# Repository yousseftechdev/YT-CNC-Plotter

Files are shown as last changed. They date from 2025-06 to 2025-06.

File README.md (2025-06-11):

# YT CNC Plotter
This is a hobby project, it's basically a Mini CNC Plotter made using small 5v stepper motors and an Arduino Nano, I'll use it to draw circuits on copper plates to essentially make DIY single layer PCBs.

## Showcase
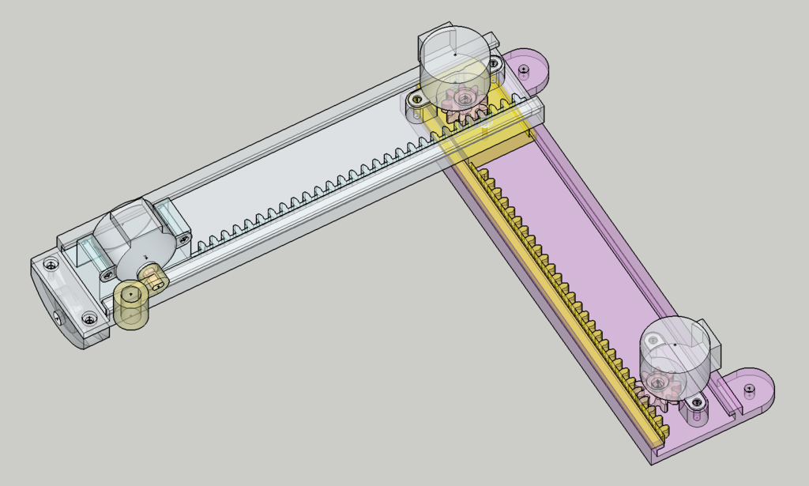
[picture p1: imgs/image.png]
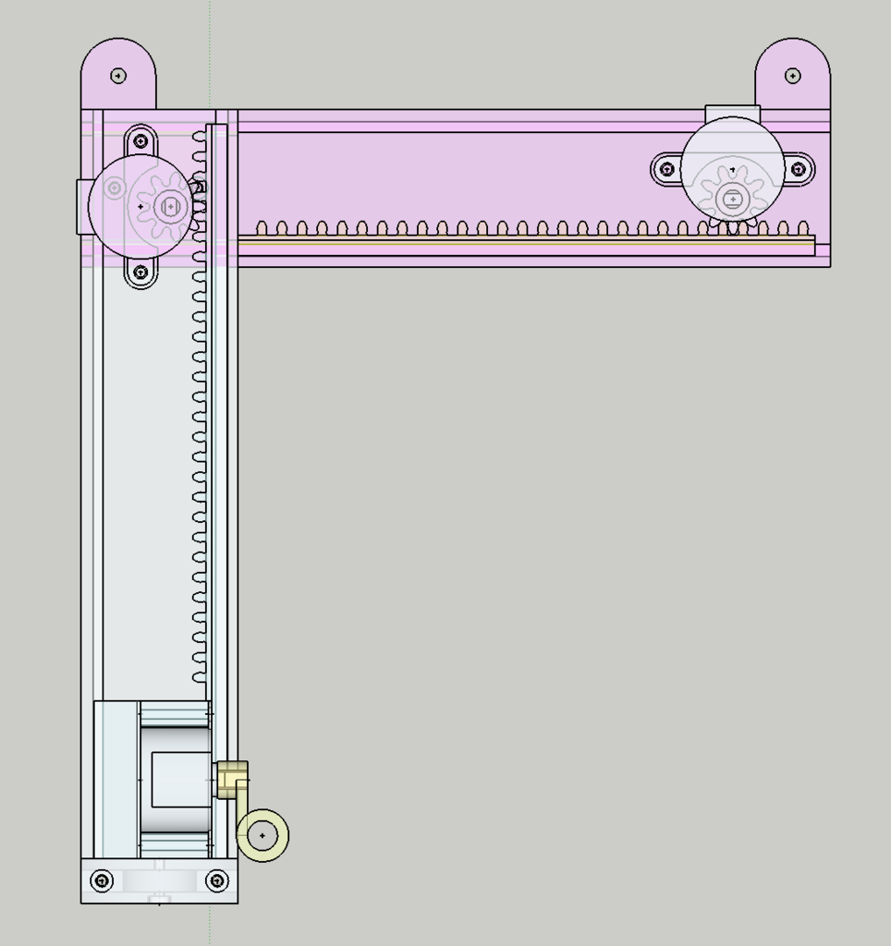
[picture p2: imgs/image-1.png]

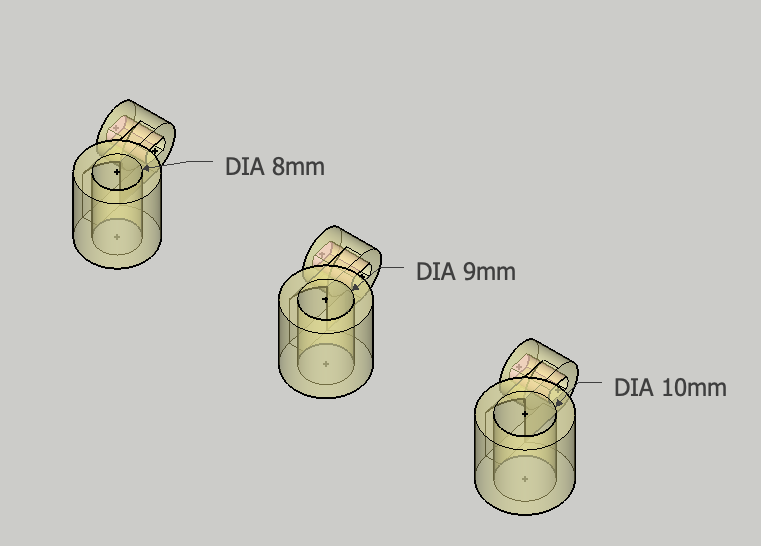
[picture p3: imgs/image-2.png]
<br>
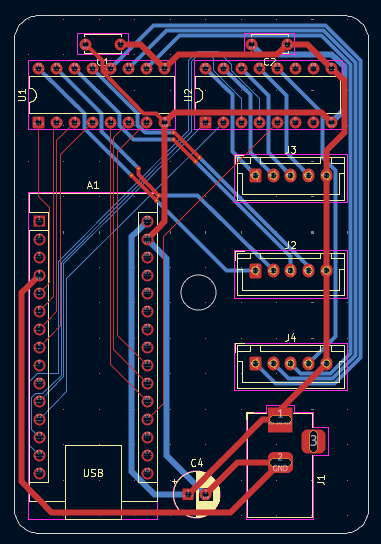
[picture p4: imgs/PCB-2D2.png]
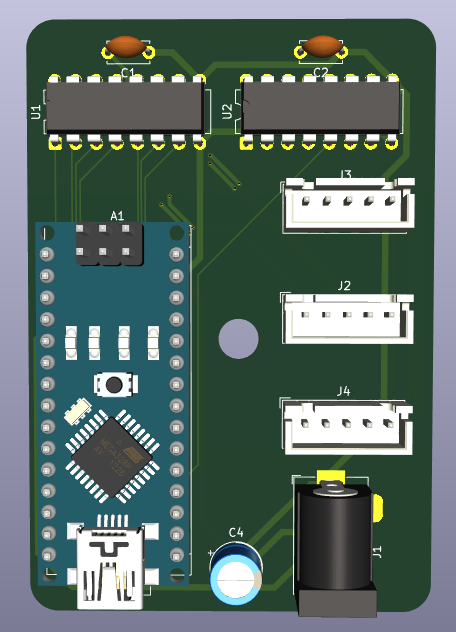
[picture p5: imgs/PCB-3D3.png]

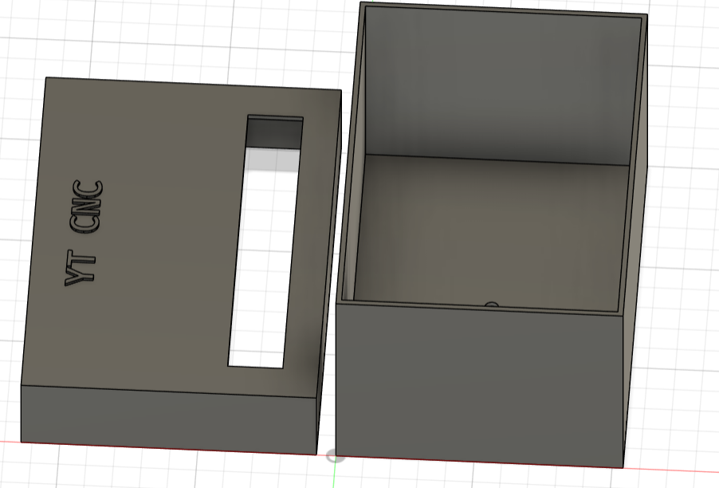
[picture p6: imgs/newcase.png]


## How does it work?
It uses gear tracks the are moved by the stepper motors, two stepper motors are used to control the X and Y position of the pen and the third motor is used to control the Z position aka the up and down movement of the pen, a script will be used to translate normal G-Code that's used in big CNC machines into something the Arduino can understand.

## How to build?
All you need to do is print the PCB and solder the components specified in the Bill of Materials (BOM) section, or if you don't feel like printing the PCB just put all the components on a breadboard and follow the schematic in my [Journal](JOURNAL.md) for the wiring, then print the frame parts and mount the stepper motors to it and boom, you're done!

## BOM:

| Name | Price | Quantity | Vendor | Link | Total Cost |
| --- | --- | --- | --- | --- | --- |
| Arduino Nano | ~ 300 EGP | 1 | Amazon Egypt | [Buy](https://www.amazon.eg/-/en/USB-Arduino-Nano-ATmega328P-Development/dp/B091CMTBF9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) | ~ 300 EGP |
| 28BYJ-48 Stepper Motor | 175 EGP | 3 | Amazon Egypt | [Buy](https://www.amazon.eg/-/en/DIY-Kit-sourcingmap-28BYJ-48-5V-Phase-Stepper/dp/B0DZXWMGWK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) | 525 EGP |
| ULN2003A Motor Driver Chips | 64 EGP | 2 | Amazon Egypt | [Buy](https://www.amazon.eg/-/en/ULN2003-Channel-Darlington-Sink-Driver/dp/B09H19L9BG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) | 128 EGP |
| 100 nF Capacitors | 45 EGP | 2 | Amazon Egypt | [Buy](https://www.amazon.eg/-/en/10Pcs-Ceramic-Capacitor-0-1uf-100nf/dp/B09HZGRMS6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) | 90 EGP |
| 100 uF Capacitor | 26.5 EGP | 1 | Amazon Egypt | [Buy](https://www.amazon.eg/-/en/Other-100uF-25V-Round-Capacitor/dp/B091D7ZC4C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) | 26.5 EGP |
| JST HX 5 Pin connector | 44 EGP | 3 | Amazon Egypt | [Buy](https://www.amazon.eg/-/en/DIY-kit-Data-Terminal-Connector-2-54mm/dp/B0F2GB82ZZ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) | 132 EGP |
| 5v Adapter | 52.25 EGP | 1 | Amazon Egypt | [Buy](https://www.amazon.eg/-/en/AC-DC-Adapter-5V-1A/dp/B091D28XJ7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) | 52.25 EGP |
| Barrel Jack | 130 EGP | 1 | Amazon Egypt | [Buy](https://www.amazon.eg/-/en/5PCS-Charging-Connector-Universal-Replacement/dp/B09RVZVZ9V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) | 130 EGP |
| Female Pin headers | 52 EGP | 1 | Amazon Egypt | [Buy](https://www.amazon.eg/-/en/Female-Pin-Header-1x40Pin-2-54mm/dp/B0CJYGZXSY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) | 52 EGP |
| 3D Printing | Depends on vendor | | | | Depends on vendor |
| PCB Manufacturing | Depends on vendor | | | | Depends on vendor |
| | | | | | Grand total:<br><br>1303.75 EGP or 26.33 USD |

## What have I learned?

I have learned so much about CAD from making this project, this has been such a great learning experience, but the most important thing I've learned is not to use Fusion 360 ever again.

Note: If you want to print the STL files please scale them down, Fusion messed up when exporting.

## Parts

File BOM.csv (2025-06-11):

Name: | Price: | Quantity: | Vendor: | Link: | Total:
Arduino Nano | ~ 300 EGP | 1 | Amazon Egypt | https://www.amazon.eg/-/en/USB-Arduino-Nano-ATmega328P-Development/dp/B091CMTBF9 | ~ 300 EGP
28BYJ-48 Stepper Motor | 175 EGP | 3 | Amazon Egypt | https://www.amazon.eg/-/en/DIY-Kit-sourcingmap-28BYJ-48-5V-Phase-Stepper/dp/B0DZXWMGWK | 525 EGP
ULN2003 Motor Driver | 64 EGP | 2 | Amazon Egypt | https://www.amazon.eg/-/en/ULN2003-Channel-Darlington-Sink-Driver/dp/B09H19L9BG | 128 EGP
100 nF Capacitors | 45 EGP | 2 | Amazon Egypt | https://www.amazon.eg/-/en/10Pcs-Ceramic-Capacitor-0-1uf-100nf/dp/B09HZGRMS6 | 90 EGP
100 uF Capacitor | 26.5 EGP | 1 | Amazon Egypt | https://www.amazon.eg/-/en/Other-100uF-25V-Round-Capacitor/dp/B091D7ZC4C?rnid=22080723031 | 26.5 EGP
JST HX 5 Pin connector | 44 EGP | 3 | Amazon Egypt | https://www.amazon.eg/-/en/DIY-kit-Data-Terminal-Connector-2-54mm/dp/B0F2GB82ZZ | 132 EGP
5v Adapter | 52.25 EGP | 1 | Amazon Egypt | https://www.amazon.eg/-/en/AC-DC-Adapter-5V-1A/dp/B091D28XJ7 | 52.25 EGP
Barrel Jack | 130 EGP | 1 | Amazon Egypt | https://www.amazon.eg/-/en/5PCS-Charging-Connector-Universal-Replacement/dp/B09RVZVZ9V | 130 EGP
Female Pin headers | 52 EGP | 1 | Amazon Egypt | https://www.amazon.eg/-/en/Female-Pin-Header-1x40Pin-2-54mm/dp/B0CJYGZXSY | 52 EGP
3D Printing | Depends on vendor |  |  |  | Depends on vendor
PCB Manufacturing | Depends on vendor |  |  |  | Depends on vendor
 |  |  |  |  | 1303.75 EGP or 26.33 USD

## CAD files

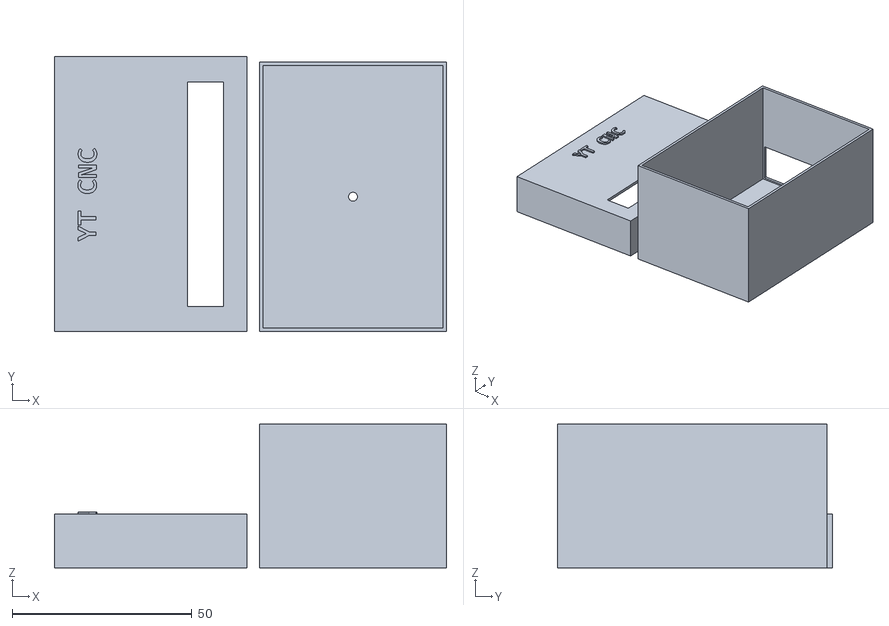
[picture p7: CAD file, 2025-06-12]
3D Print Files/PCB-Case2.stl
109.0 x 76.5 x 40.0

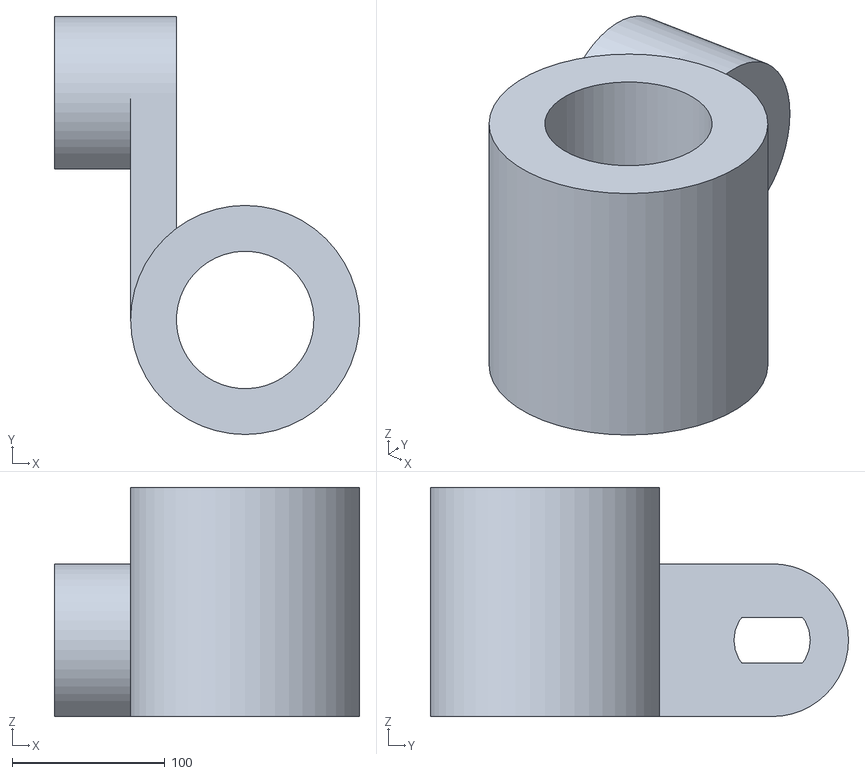
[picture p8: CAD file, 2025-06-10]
3D Print Files/penHolder2.stl
200.0 x 273.7 x 150.0

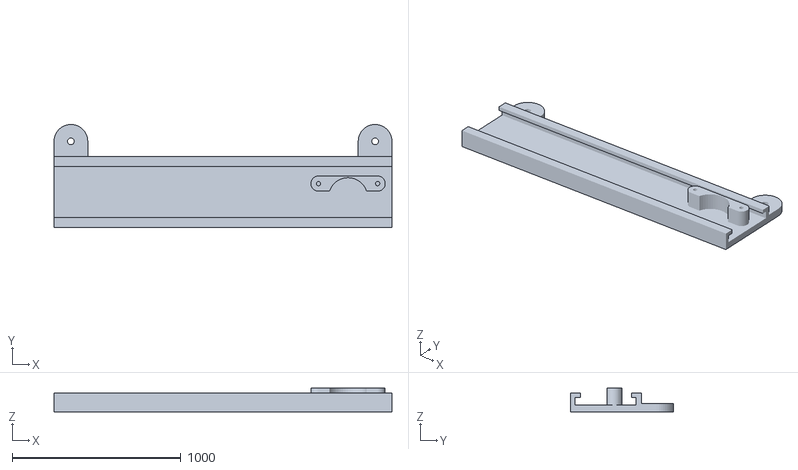
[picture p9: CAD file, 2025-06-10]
3D Print Files/base.stl
2000.0 x 610.0 x 140.0

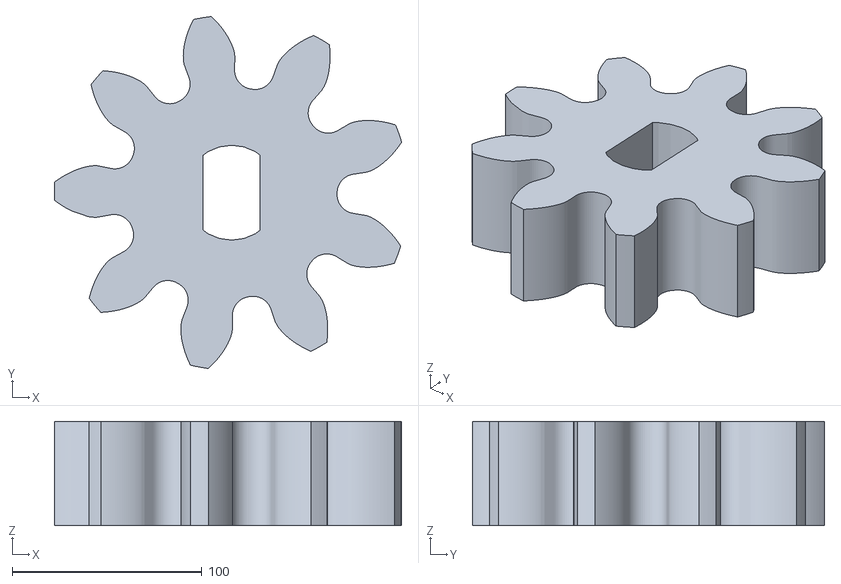
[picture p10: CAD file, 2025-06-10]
3D Print Files/gear.stl
183.1 x 185.6 x 55.0

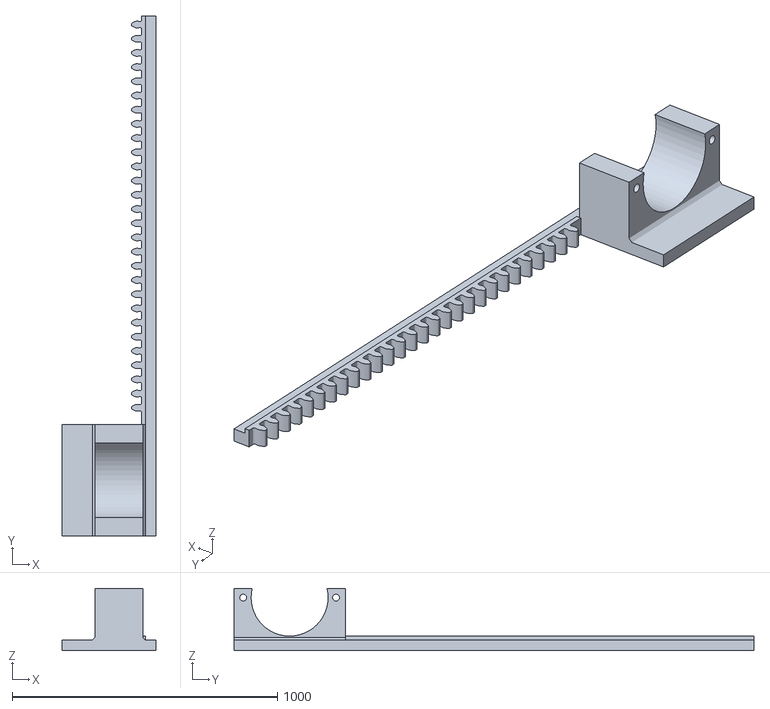
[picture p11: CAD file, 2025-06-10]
3D Print Files/track2.stl
355.0 x 1960.0 x 235.0

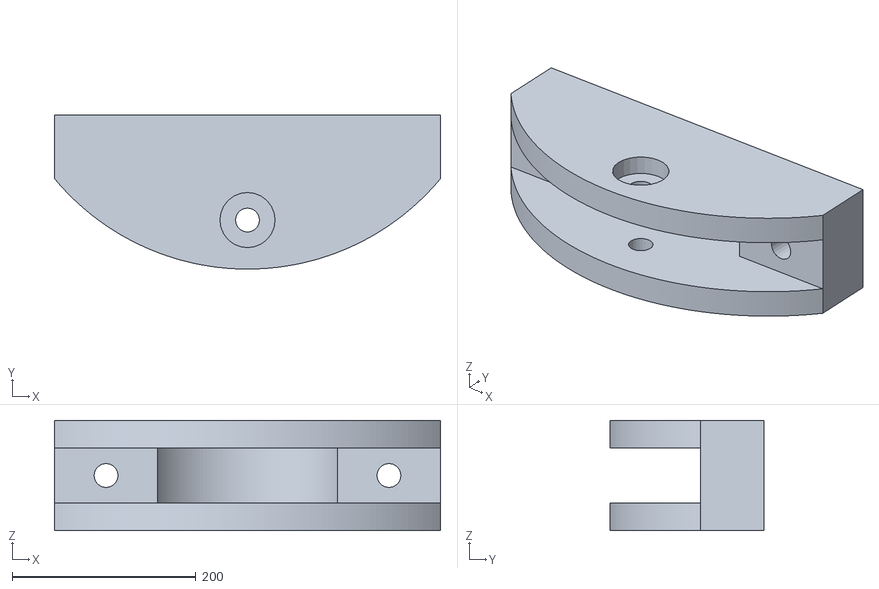
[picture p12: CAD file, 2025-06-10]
3D Print Files/holder.stl
420.0 x 167.7 x 120.0

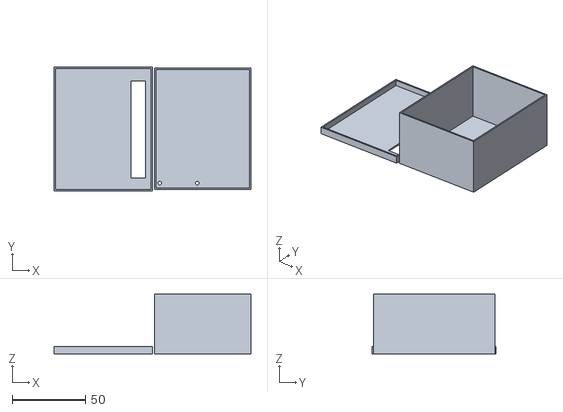
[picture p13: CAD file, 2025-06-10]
3D Print Files/PCB-Case.stl
134.5 x 84.8 x 40.9

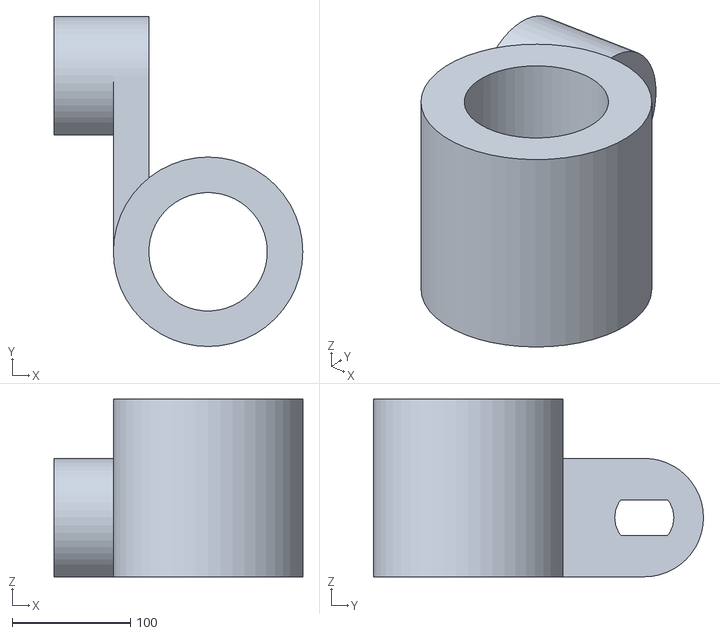
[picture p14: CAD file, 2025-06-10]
3D Print Files/penHolder3.stl
210.0 x 278.7 x 150.0

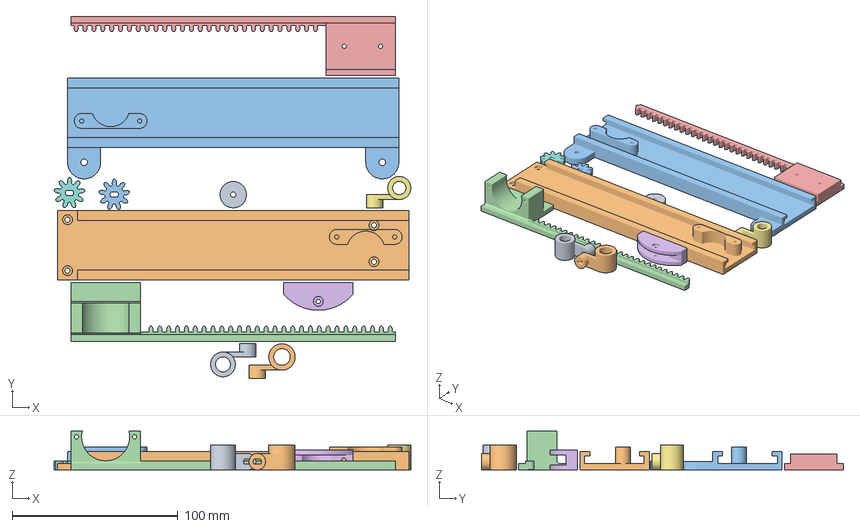
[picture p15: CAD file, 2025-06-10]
3D Print Files/AIO.3mf
215.4 x 218.6 x 23.5 mm
7.stl
1.stl
4.stl
2.stl
3.stl
6.stl
8.stl
5.stl
9.stl
A.stl
5.stl(1)

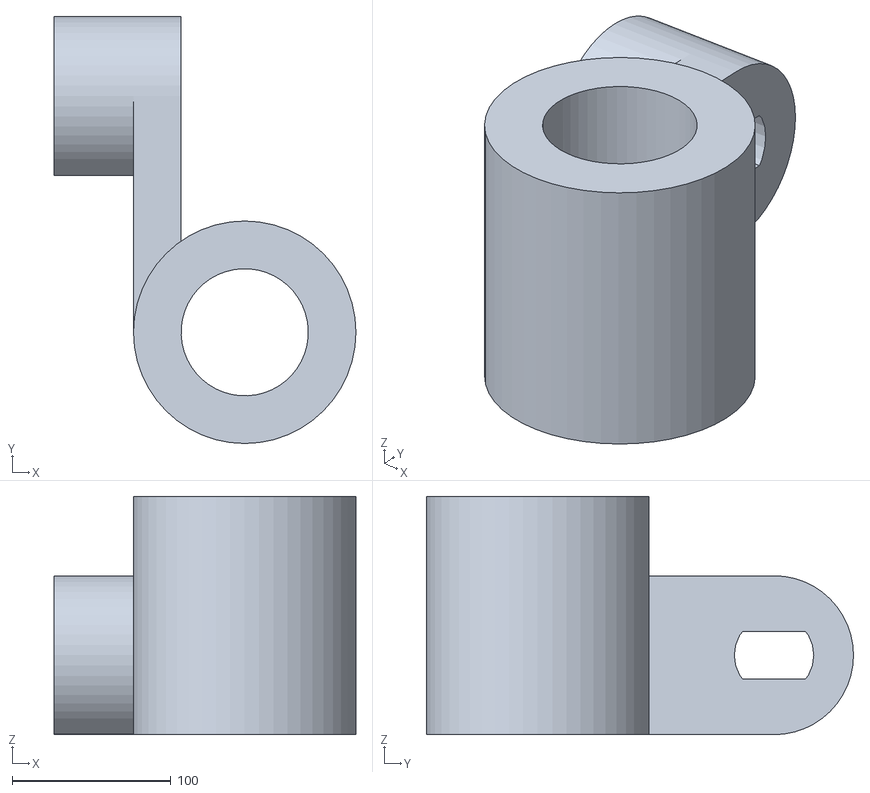
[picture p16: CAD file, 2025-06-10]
3D Print Files/penHolder.stl
190.0 x 268.7 x 150.0

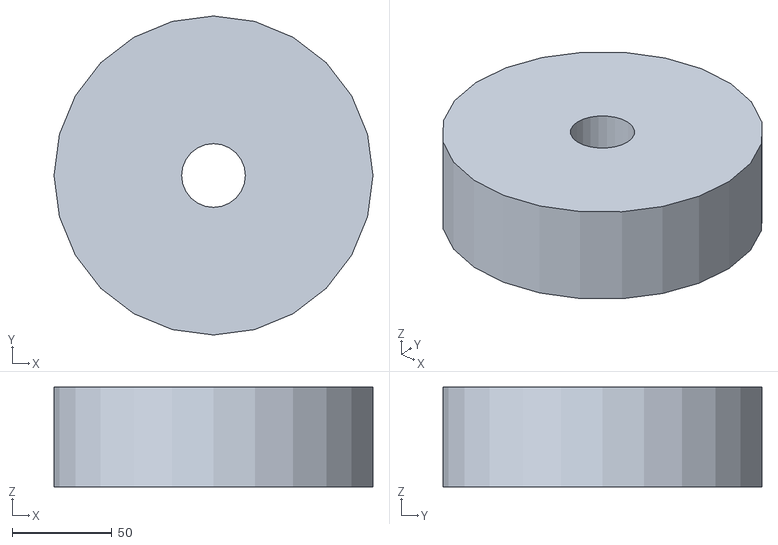
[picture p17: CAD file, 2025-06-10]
3D Print Files/wheel.stl
160.0 x 160.0 x 50.0

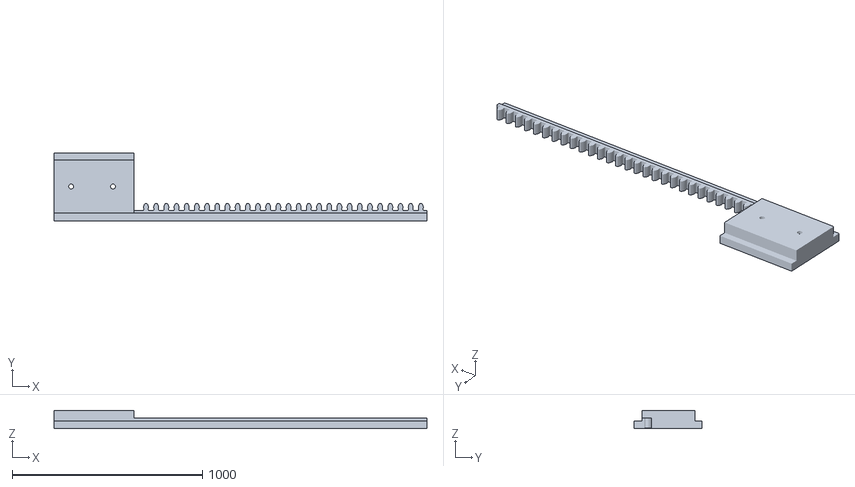
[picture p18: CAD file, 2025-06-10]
3D Print Files/track1.stl
1960.0 x 355.0 x 95.0

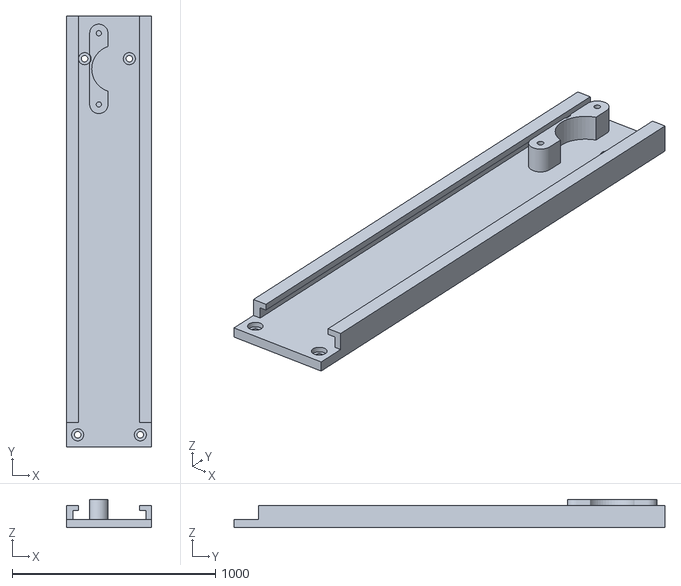
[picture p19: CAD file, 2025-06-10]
3D Print Files/base2.stl
420.0 x 2120.0 x 140.0

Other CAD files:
3D Models/PCB-Case.f3d
3D Models/PCB-Case2.f3d
3D Models/base.f3d
3D Models/base2.f3d
3D Models/gear.f3d
3D Models/holder.f3d
3D Models/penHolder1.f3d
3D Models/penHolder2.f3d
3D Models/penHolder3.f3d
3D Models/track1.f3d
3D Models/track2.f3d
3D Models/wheel.f3d

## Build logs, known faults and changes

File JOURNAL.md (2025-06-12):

---
title: "YT CNC Plotter"
author: "Youssef Tech"
description: "A mini CNC Plotter to trace PCB designs on copper plates"
created_at: "2025-06-09"
---

Total time spent: 21 hours and 49 minutes
Total cost of parts (without 3D printing): 1,307.75 EGP or 26.33 USD
Approx. 3D printing cost: 315 EGP or 6.35 USD

# [2025-06-09] [Time spent: 6 hours] Day 1: Brainstorming, and first steps
First let's get the idea of my project cleared up, I wanna make a mini CNC plotter that I can use to draw/trace PCBs on copper plates so that I can manufacture simple 1 layer PCBs at home.

I'm trying to imagine how this thing would work, I was thinking of belt drives at first, but then I felt that it wouldn't be very accurate.

For now I'm making a list of the components I'll be using.

So I found a similar project online that I'll be taking inspiration from for this project, and it utilizes the following components

The list:
- Arduino Nano for control
- 3x Stepper motors (Model: 28BYJ-48)
- 3x Stepper motor drivers (Model: ULN2003)
- 3D printed frame

These are the main components at least, I didn't think of the other small components I'll need, like capacitors and stuff

Started designing the PCB in KiCad, and making a BOM as I go.

Finished PCB design, FINALLY. The pcb took HOURS to finish, made me wish I had gone with the breadboard method instead. Hoping it works when I actually order it 😭🙏🏻

The PCB has the 3 motor drivers connected to the GPIO on the Arduino, and there are some capacitors to minimize flyback voltage from the motors, I added a barrel jack to power the Arduino and the motors, they are wired in parallel though and I'm not sure if that's dangerous.

And also I will not be soldering the Arduino onto the board because that would be a waste of a perfectly good dev board so I'll use female pin sockets in its place during assebly

PCB Images:<br>
Schematic:<br>
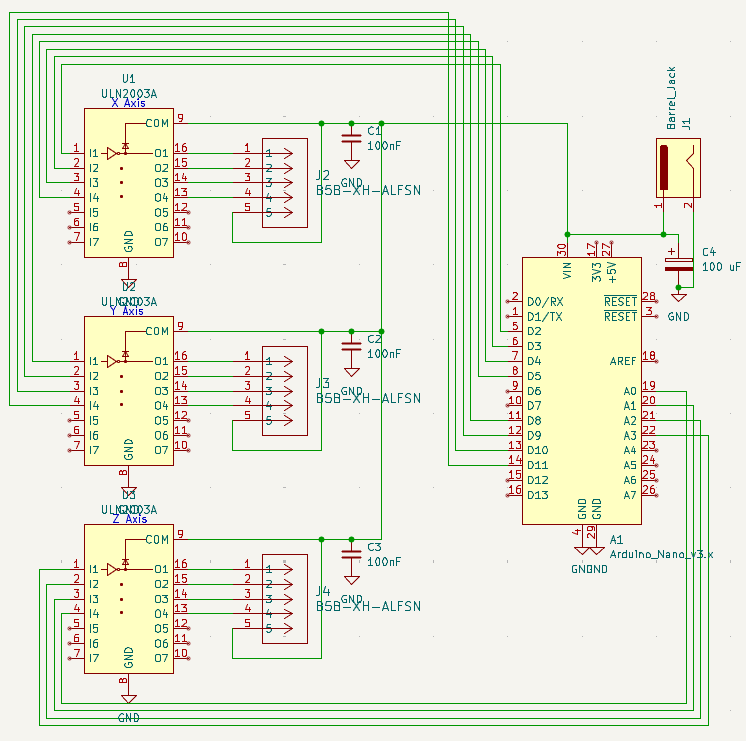
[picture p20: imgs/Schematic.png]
shematic


PCB Design:<br>
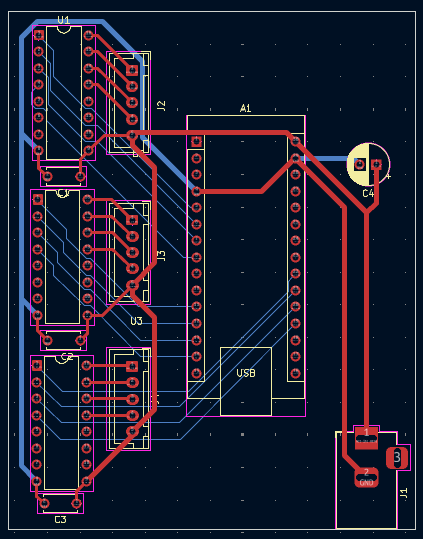
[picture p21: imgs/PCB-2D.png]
design


PCB Model:<br>
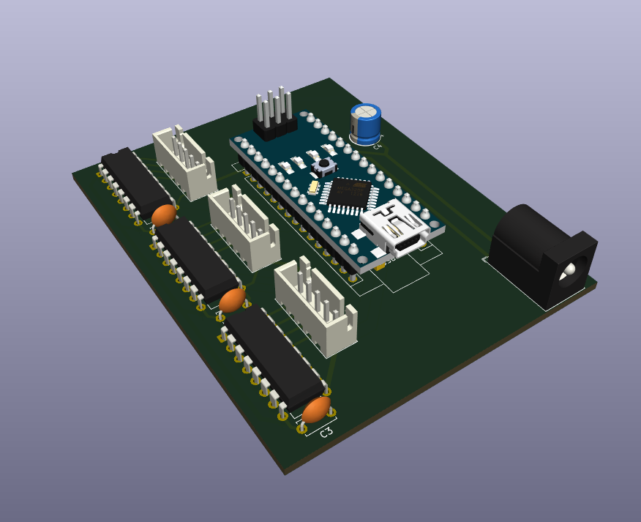
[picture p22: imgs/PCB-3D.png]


# [2025-06-10] [Time spent: 9 hours and 25 minutes] Day 2: 3D modeling
It's 6:35 AM as of writing this, I haven't slept yet since finishing the PCB (started Day one at 10 PM yesterday, finished at 4:45 AM). I've decided to start working on the 3D models I'll need for this project, idk anything about CAD and idk how I'm gonna get the motors to move the pointer/pen correctly, so I'm gonna start by making a case for the control board I designed yesterday.

The program I've decided to use is Fusion 360, no specific reason why I chose it. Currently watching a tutorial on how to use it since it's my first time in a CAD software.

Took some measurements from the PCB in KiCad so I can make the case as much of a tight fit as I can.

Put some mounting holes in the PCB and put some holes in the case for the PCB to be screwed into.

Man I didn't realize Fusion was such a pain 😫, all the YouTubers made it seem like the best CAD software ever or sum.

CREATED A CUBE 🔥🔥🔥<br>
HOLLOWED THE CUBE 🔥🔥🔥

I left a 1 mm clearance between the case walls and the and the PCB itself, and made a lid.

Added opening for motor cables (Almost forgot that)

Finally done with the case, can't beleive I spent that much time on this case, it is now 7:57 AM, almost one and a half hours on this:<br>
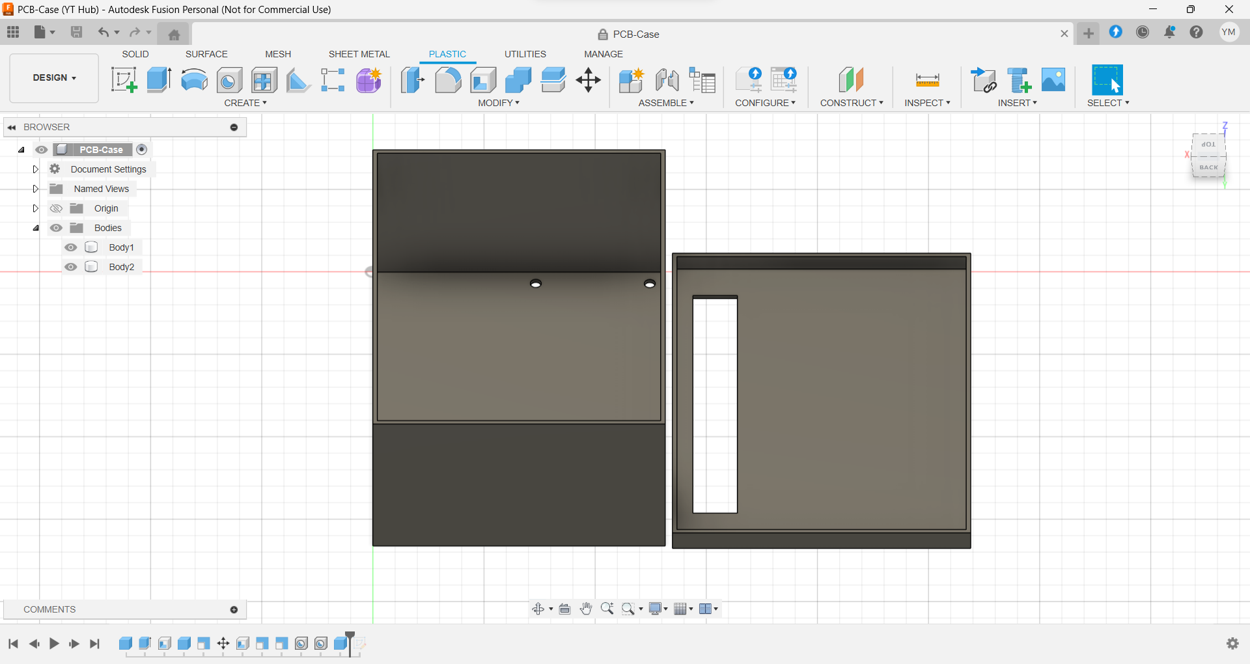
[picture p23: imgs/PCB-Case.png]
case


Aaaand now for the task I've been putting off since the start... the FRAME 💀!!!

Idk how to get started on this tbh, but I'll try, maybe I'll look at similar projects to get an idea about how they calculate the gear teeth number and all those details.

After looking at multiple projects I noticed that most of them used a 9 tooth gear to drive the axis, so I guess I'll be using the same number.

HOW DO I CREATE A GEAR in Fusion!!?!?!

Starting to get sick of tutorials here<br>
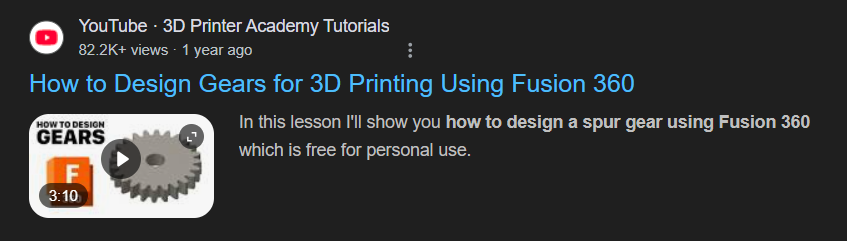
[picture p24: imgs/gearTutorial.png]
tutorial


Ok I'm getting there but I'm trying to figure out how to get the shape of the hole in the gear to be like the shape of the shaft of the motor, the gear looks like this for now:<br>
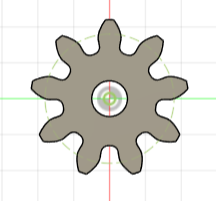
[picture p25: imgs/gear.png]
gear


And this is what the shaft shape looks like, it's called a "Double D" shape:<br>
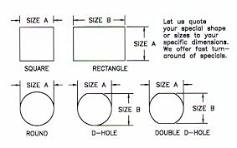
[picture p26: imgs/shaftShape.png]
shaft


FINALLY GOT IT, after lots of tutorials, I finally got the gear right:<br>
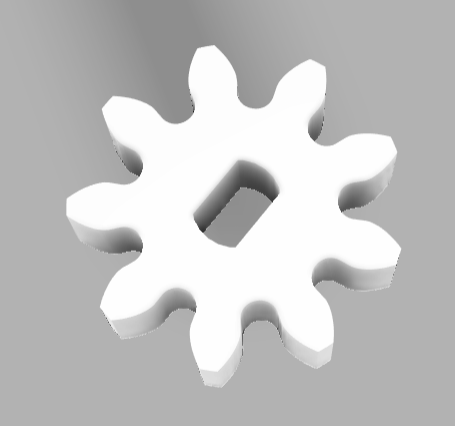
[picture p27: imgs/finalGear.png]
final-gear


Now comes the easy part, the rails, since I already know the gear's properties I can just use the same ones on the rail/track and they'd mesh together perfectly.

This is the base track, it has mounting holes and a place to mount the motor with the gear attached to it:<br>
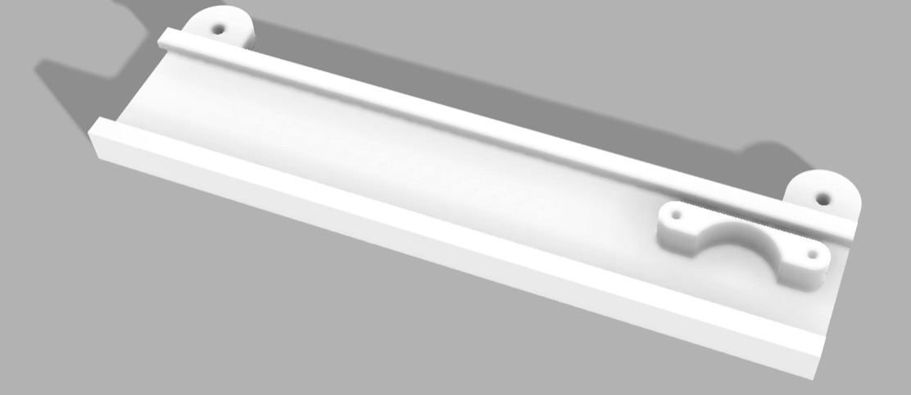
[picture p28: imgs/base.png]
base


And this is the primary gear track, it meshes with the gear on the motor mounted to the base to control the Y-Axis, it also has a platform to mount the X-Axis base onto it:<br>
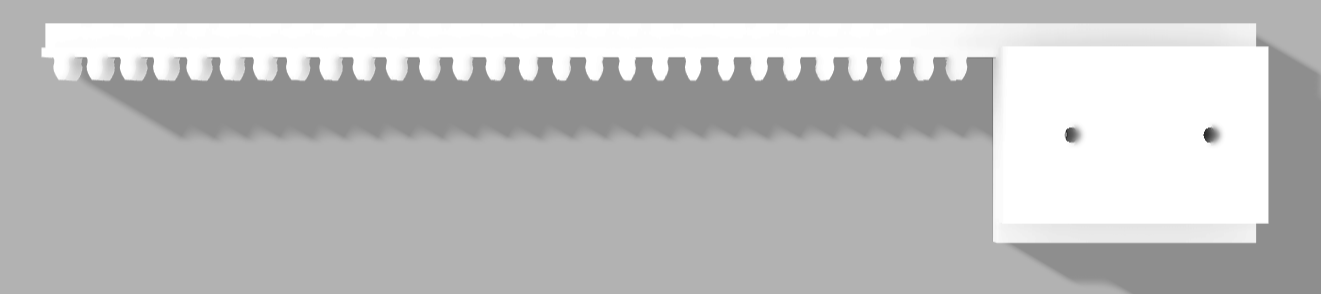
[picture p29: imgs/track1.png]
track1


Half the work is now done, the next few parts are going to be easier to model since they're just slightly modified versions of the previous parts.

The X-Axis base is now FINISHED, YIPPEE, it will be mounted on the primary track and will be used to hold the secondary track which will move the Z-Axis motor AKA the Pen motor:<br>
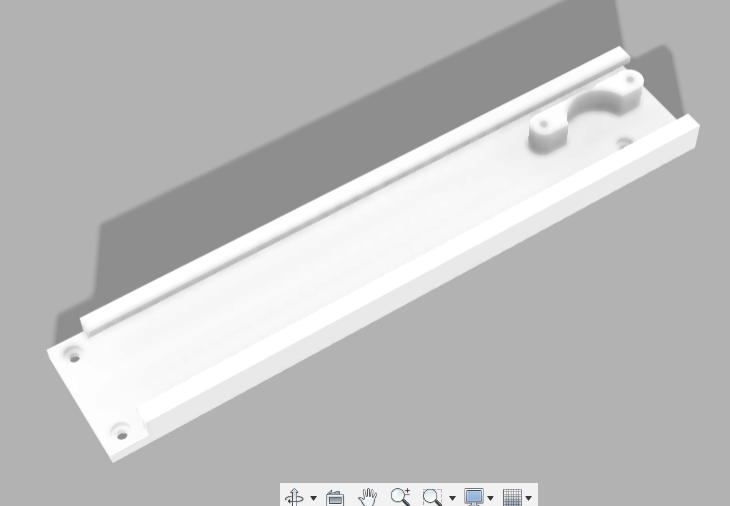
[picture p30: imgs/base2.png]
base2


The secondary track is basically the primary track but with a motor mount instead of the base mount:<br>
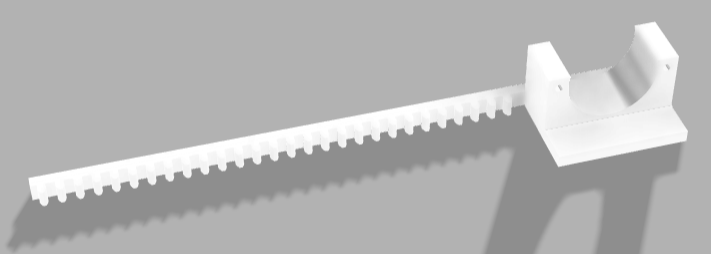
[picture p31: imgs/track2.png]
track2


This pretty much concludes the main stuff, like these could somewhat work on their own, but there are some finishing touches I wanted to add.

If you haven't noticed at the end of the X-Axis base there are mounting holes for something, they're for a roller/wheel, it acts as a stand to reduce friction between the X-Axis base and the Y-Axis base, and prevents friction with the surface the CNC Plotter is mounted on by having a rolling wheel, it consists of two parts, the wheel itself and its holder:
- Holder:<br>
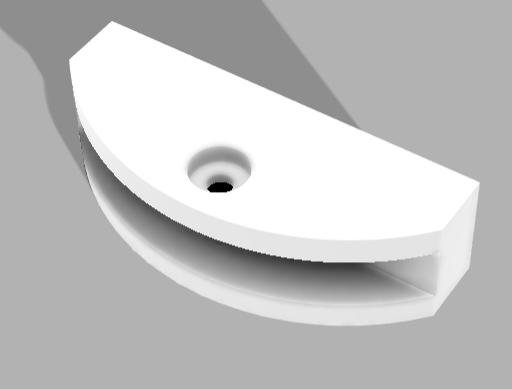
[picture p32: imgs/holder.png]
holder


- Wheel:<br>
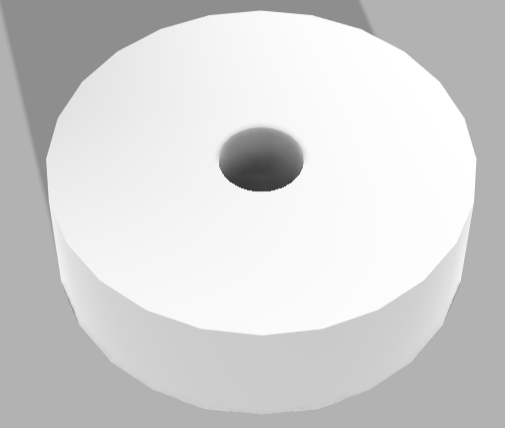
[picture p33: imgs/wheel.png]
wheel


Now, all that's left is the Pen holder, it's a combination of two hollow cylinders connected by a rectangle, one of the cylinders has the Double D hole cutout to make it fit onto the Z-Axis motor, I've design multiple different sizes so it can fit all pens/pencils:
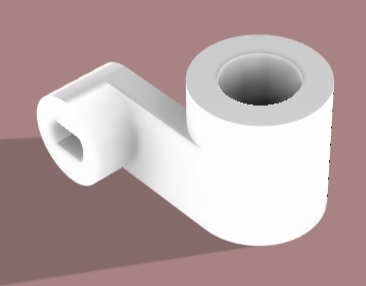
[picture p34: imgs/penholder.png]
penholder


After the parts arrive and the frame gets printed I'll get the chance to write the firmware for this project.

# [2025-06-11] [Time spent: 4 Hours and 24 minutes] Day 3: Finalizing
This is probably the last day I'll be working on this, today is just gonna be cleaning up the journal and adding any missing info, checking on the PCB to see if I did something wrong or need to add anything, it is now 8:36 AM, getting started.

Welp after reviewing the PCB and getting the help of HC slack member StrawberryPuding, I realized I only need two ULN2003 chip not three, so I spent the past 2 hours (it's 10:30 rn) modifying the schematic and rerouting the entire PCB, I was able to use two ULNs instead of three and made the board smaller and more compact, I was able to shave off 150.43 EGP or 3.04 USD from my BOM, here are the pics of the new PCB:

Schematic:
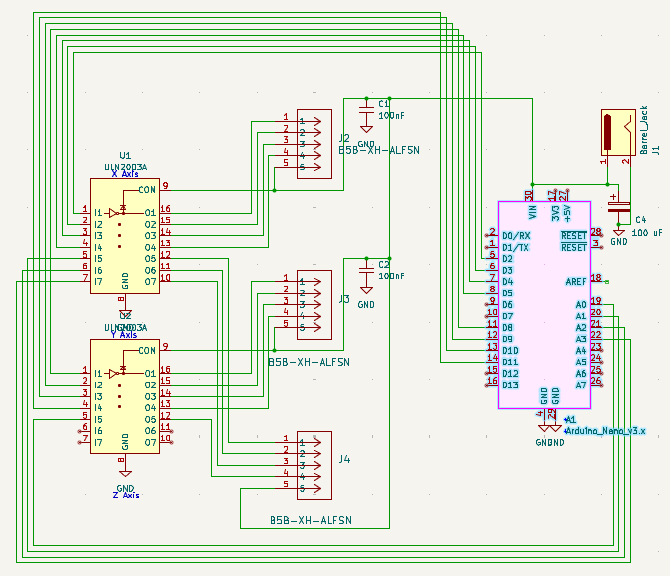
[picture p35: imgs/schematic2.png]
schematic2


PCB Design:
design2

PCB Model:
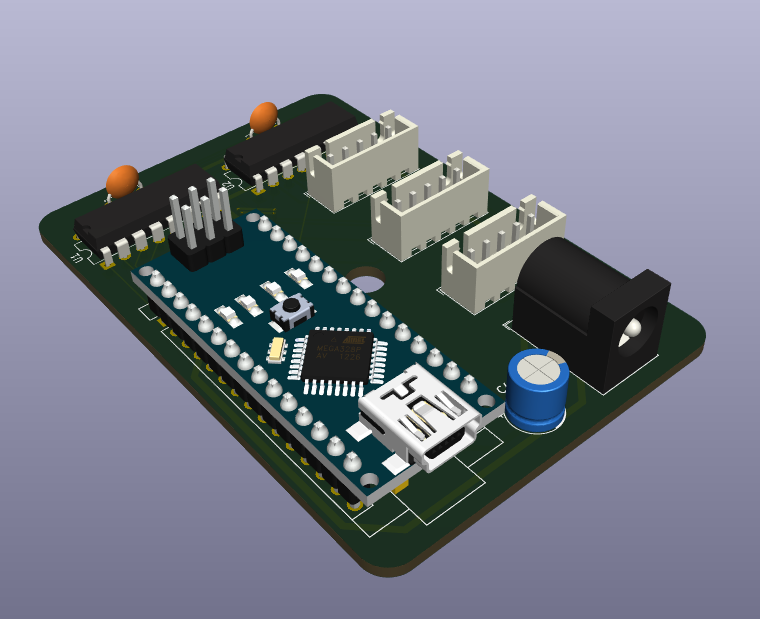
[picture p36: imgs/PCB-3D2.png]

model2

The PCB is smaller, you know what that means, right? back to Fusion I go!
I only put one mounting hole on the pcb this time to make designing the box easier.

The PCB is 73x50 mm so I'll make the case 75x52 (Exterior area)

OMG FUSION KEEPS CRASHING MY PC ISTG, fusion has crashed 4 times in the past hour and I can't get anything done from how much it's slowing my pc down.

Took a break from Fusion a bit cause every time I click anything it the app crashes and decided to fill the blank space on the PCB by adding a power LED, I know, pointless, but I just wanted to add something.

After Fusion finally launched I finished the new PCB case and I learned how to use the emboss feature to write YT CNC on it (YT stands for Youssef Tech, my username)
newcase

summary of what I did today:
- Redesign the PCB
- Redesign the case for the PCB
- Create the README.md file
- Review the frame models to see if I can improve anything even slightly

Hoping everything works correctly when printed

Note: If you want to print the STL files please scale them down, Fusion messed up when saving.

# [2025-06-12] [Time spent: 2 hours] Day 4: Fixing a stupid mistake
I know, I know, I said yesterday would be the last time I work on this, but as I was getting into bed yesterday, I realized something... I DIDN'T MAKE OPENINGS IN THE PCB CASE FOR THE CABLES.

Opening Fusion360 for (hopefully) the last time.

PC is already overheating from this app, idk if my PC is too weak or Fusion is just a menace

Tbh idk how I'll make the opening for the USB port on the Arduino since I'm gonna be using female pin sockets to place the Arduino on the board

Just cut out a big rectangle from the side, done, yippee

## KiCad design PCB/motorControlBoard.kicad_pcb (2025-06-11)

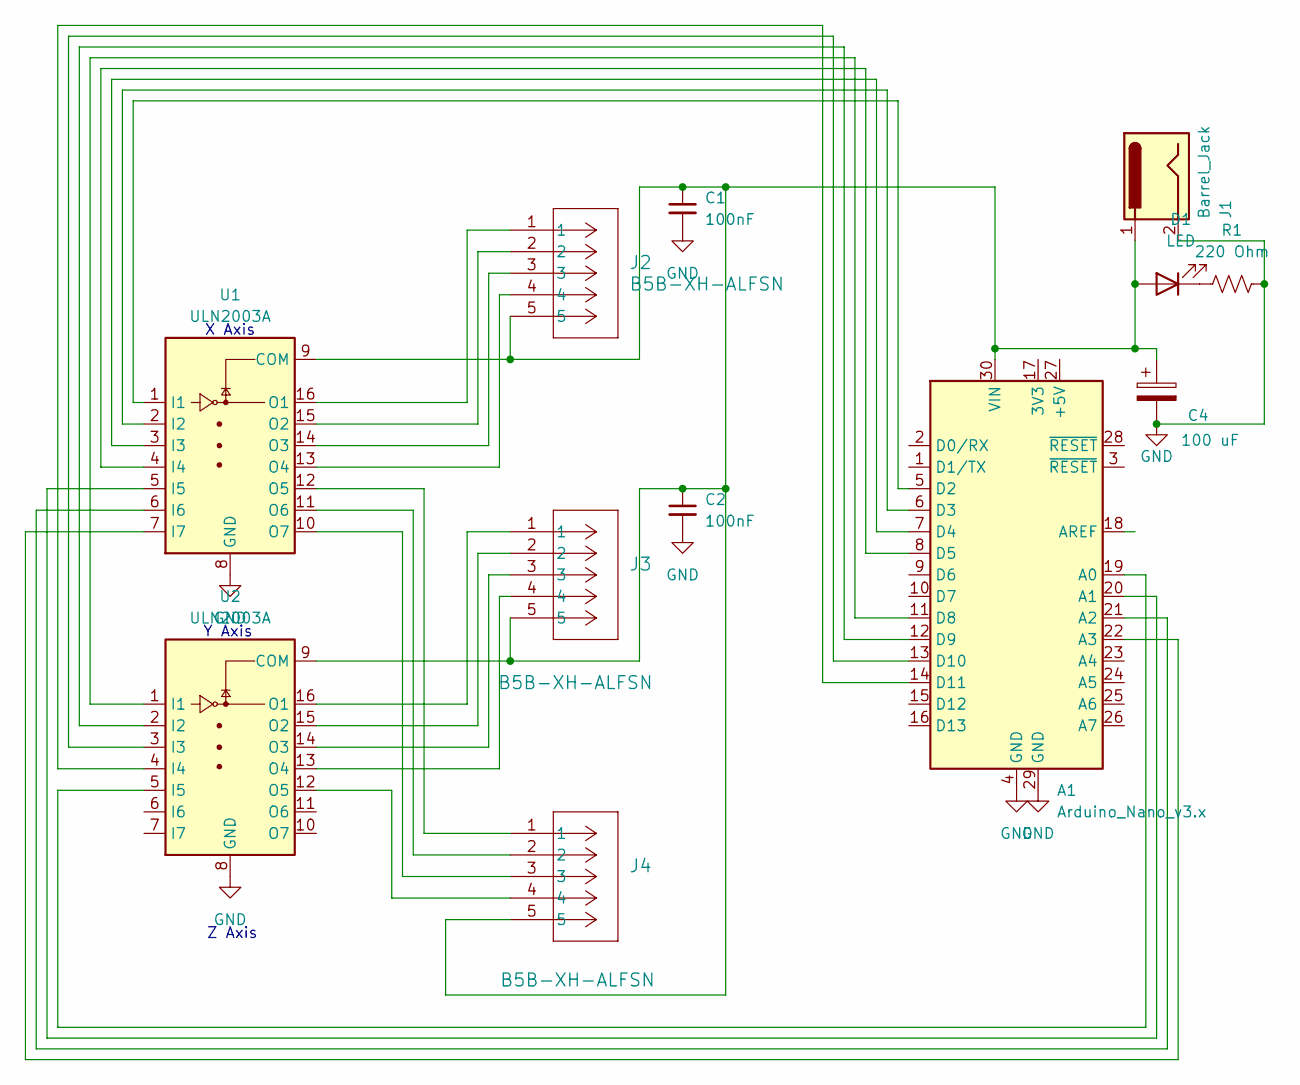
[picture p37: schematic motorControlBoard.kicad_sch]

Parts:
A1: Arduino_Nano_v3.x; Arduino_Nano
C1, C2: 100nF; C_Disc_D5.0mm_W2.5mm_P5.00mm
C4: 100 uF; CP_Radial_D6.3mm_P2.50mm
D1: LED; LED_D5.0mm
J1: Barrel_Jack; BarrelJack_Horizontal
J2, J3, J4: B5B-XH-ALFSN; JST_XH_B5B-XH-A_1x05_P2.50mm_Vertical
R1: 220 Ohm; R_Axial_DIN0204_L3.6mm_D1.6mm_P7.62mm_Horizontal
U1, U2: ULN2003A; DIP-16_W7.62mm

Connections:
GND: A1.4 (GND), A1.29 (GND), C1.2, C2.2, C4.2, J1.2, R1.2, U1.8 (GND), U2.8 (GND)
unnamed: A1.19 (A0), U2.5 (I5)
unnamed: A1.20 (A1), U1.5 (I5)
unnamed: A1.21 (A2), U1.6 (I6)
unnamed: A1.22 (A3), U1.7 (I7)
unnamed: A1.5 (D2), U1.1 (I1)
unnamed: A1.6 (D3), U1.2 (I2)
unnamed: A1.7 (D4), U1.3 (I3)
unnamed: A1.8 (D5), U1.4 (I4)
unnamed: A1.11 (D8), U2.1 (I1)
unnamed: A1.12 (D9), U2.2 (I2)
unnamed: A1.13 (D10), U2.3 (I3)
unnamed: A1.14 (D11), U2.4 (I4)
unnamed: A1.30 (VIN), C1.1, C2.1, C4.1, D1.2 (A), J1.1, J2.5, J3.5, J4.5, U1.9 (COM), U2.9 (COM)
unnamed: D1.1 (K), R1.1
unnamed: J2.1, U1.16 (O1)
unnamed: J2.2, U1.15 (O2)
unnamed: J2.3, U1.14 (O3)
unnamed: J2.4, U1.13 (O4)
unnamed: J4.1, U1.12 (O5)
unnamed: J4.2, U1.11 (O6)
unnamed: J4.3, U1.10 (O7)
unnamed: J3.1, U2.16 (O1)
unnamed: J3.2, U2.15 (O2)
unnamed: J3.3, U2.14 (O3)
unnamed: J3.4, U2.13 (O4)
unnamed: J4.4, U2.12 (O5)

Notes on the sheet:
Y Axis
X Axis
Z Axis

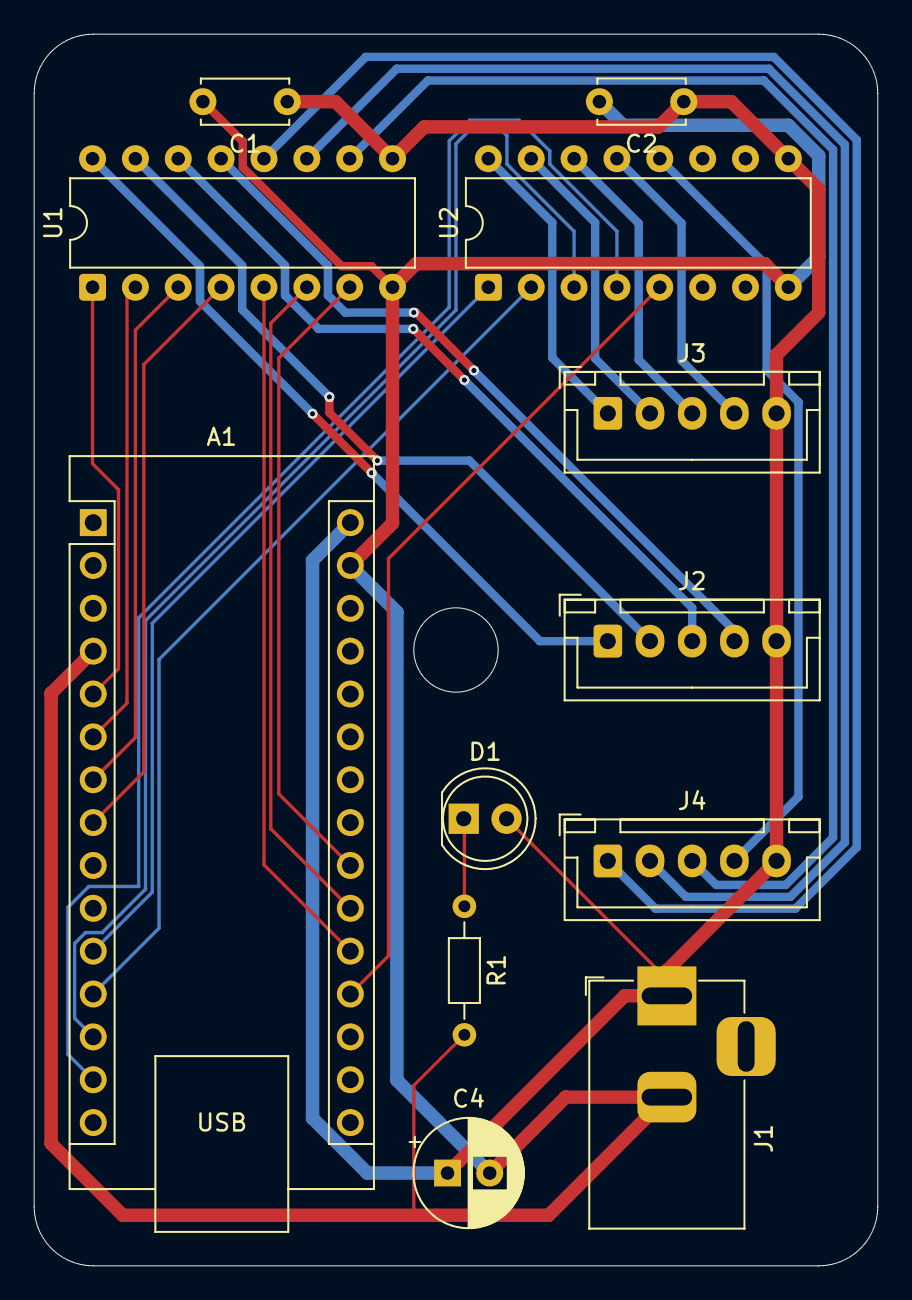
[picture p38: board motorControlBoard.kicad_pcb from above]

Board: 2 copper layers, 50.0 x 73.0 mm, 12 parts (0 on the bottom side), 27 nets.

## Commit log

2025-06-09 Made parts list and designed controller PCB
    [BOM.csv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]
2025-06-10 correction to last commit
    [BOM.csv, motorControlBoard.kicad_pcb, motorControlBoard.kicad_sch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]
2025-06-10 Refined PCB and finished frame
    [AIO.3mf, BOM.csv, PCB-Case.f3d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]
2025-06-11 final (i think)
    [BOM.csv, PCB-Case2.f3d, PCB-Case2.stl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]
2025-06-11 final final final
    [motorControlBoard.kicad_pcb]
2025-06-11 Adding submission requirements
    [BOM.csv]
2025-06-12 port holes in the case
    [PCB-Case2.f3d, PCB-Case2.stl]
